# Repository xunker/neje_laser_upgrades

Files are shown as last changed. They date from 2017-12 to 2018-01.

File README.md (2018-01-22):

# neje-laser-upgrades
How-to's and resources for upgrading the NEJE (also sold under the HICTOP brand, and others) desktop USB laser engraver to full GRBL compatibility by replacing
the electronics.

Last updated January, 2018.

## Full grbl upgrade with Arduino CNC Shield

### Videos

I have uploaded a video of the whole upgrade process at [youtu.be/2rbzI-d-bOA](https://youtu.be/2rbzI-d-bOA).

A second video with specific focus on the wiring, and that covers use of a
MOSFET to switch the laser, is also available at [https://youtu.be/MuKYvifYnYs](https://youtu.be/MuKYvifYnYs).

### Links to resources

#### Software-only upgrade

If you are lucky enough to have a machine that can be upgraded without replacing
the board, you can follow [these instructions](http://diyhpl.us/laser_etcher/NEJE_Laser_Etcher/)
to flash a new version of grbl to it.

#### Hardware

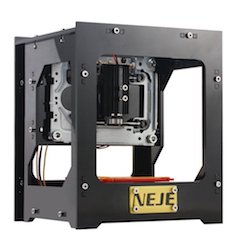
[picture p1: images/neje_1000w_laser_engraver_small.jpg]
NEJE DK-8-KZ Engraver


The engraver pictured above and in the video: [KKmoon NEJE DK-8-KZ 1000mW](https://www.amazon.com/gp/product/B01EACK7UG/ref=oh_aui_detailpage_o05_s02)

The Arduino shield used to control the steppers: [Arduino CNC Shield](http://blog.protoneer.co.nz/arduino-cnc-shield/).
I think I mistakenly referred to this as "grblshield" in the video.

[Arduino Uno](https://www.arduino.cc/en/Main/ArduinoBoardUno), the board that connects to the shield above.

[Laser focus adjustment ring](http://www.thingiverse.com/thing:1939313).

[IRF520 module](https://www.amazon.com/gp/product/B00Z8UF6AQ), the board that
controls power to the 5V laser.

#### Software

[Universal Gcode Sender](https://github.com/winder/Universal-G-Code-Sender) -
Used to send commands to the laser.

[J Tech Photonics Laser Tool](https://jtechphotonics.com/?page_id=2012) -
Used to convert images to laser commands.

#### Wiring diagrams and schematics

##### Connecting PC power supply to Arduino and Shield

The CNC shield can accept any DC voltage from 12V to 36V. Because the stepper
motors used here are very small, the 12V does not need to be high amperage;
500ma or larger will probably be sufficient.

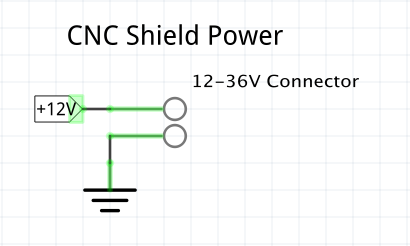
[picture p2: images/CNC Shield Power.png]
CNC Shield Power schematic


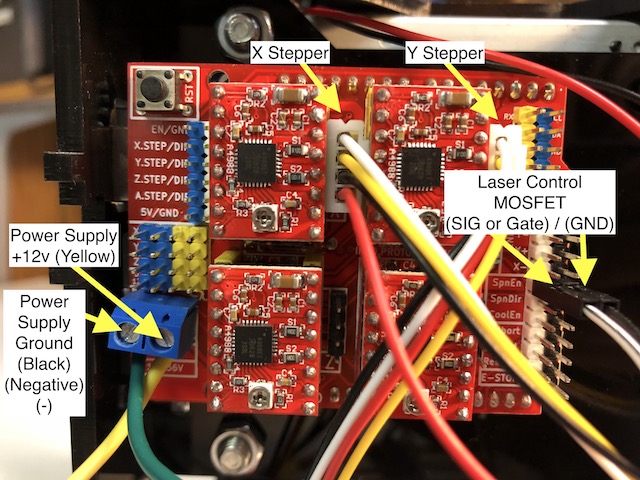
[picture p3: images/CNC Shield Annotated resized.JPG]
CNC Shield Connections annotated


To power the upgrade, I used a power supply designed to run an internal PC
hard drive, although a full-size PC power supply would work.

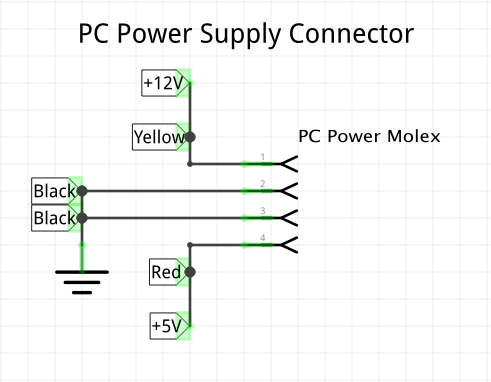
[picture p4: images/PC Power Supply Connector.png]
PC Power Supply Molex schematic


The most important part of the power supply is that is can give 5V at several
amps to power the laser.

The CNC shield electronics can then be powered from 5V as well, but I chose
to power them from the 12V rail of the power supply. If you choose to do that,
you will want to adjust the current-limit on the drivers to avoid damaging the
stepper motors. Details of how to do this are in the video.

##### Connecting stepper motors to the shield

The connector for the stepper motors are between the "drivers" (the red square
  circuit boards [in this image](images/CNC%20Shield%20Annotated%20resized.JPG).

With the white wire facing up, match the 4-pin connector on the cable to the
4-pin connector on the board for both the X- and Y-axis.

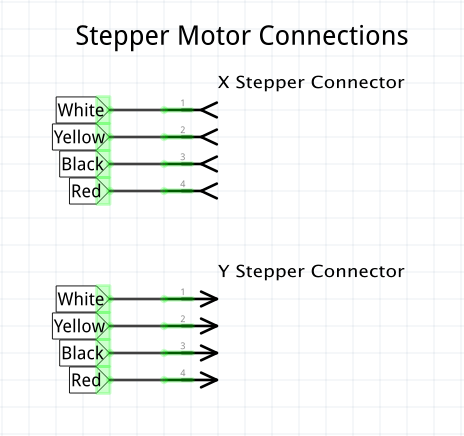
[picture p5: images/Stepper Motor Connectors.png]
Stepper motor connections


##### Connecting laser to power supply and CNC shield

The `SPNEN` (SPiNdle ENable) pin on the shield cannot power the laser itself, so
I use a circuit with a transistor to power the laser from the power supply, but
still allow it to be turned on and off by the CNC shield.

First, you will connect the positive wire of the laser (coloured red on mine) to
the 5V power line from your power supply. It *MUST* be 5V, any more will damage
the laser!

We will switch the laser on and off by connecting or disconnecting the
negative/ground wire. This technique is known as "[low-side switching](https://learn.sparkfun.com/tutorials/transistors/applications-i-switches)".

Here are two ways to do it, though there are probably other ways too. I
recommend using a MOSFET over a TIP120. But if you only have a TIP120 it will
still work though your laser power may suffer.

###### MOSFET circuit

An efficient way to switch the laser on and off is to use an N-Channel Power
MOSFET. Currently I am using an [IRF520 module like this one](https://www.amazon.com/gp/product/B00Z8UF6AQ), but this is not designed for logic-level switching so if you have the option I would
recommend using [a logic-level MOSFET](https://www.mouser.com/ProductDetail/512-FQU13N10LTU) instead.

But, regardless of the voltage, if you want to solder one yourself then the
circuit will look something like this:

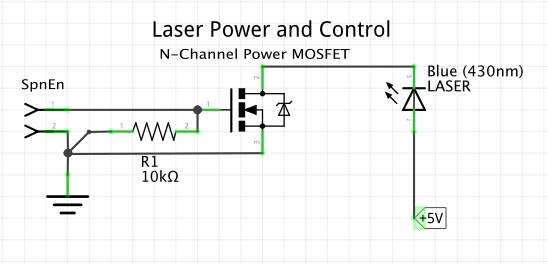
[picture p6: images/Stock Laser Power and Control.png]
MOSFET Laser Trigger schematic


This will switch the laser on and off with a minimum of voltage loss.

If you use the same IRF520 module that I did, here is how the wires are
connected:

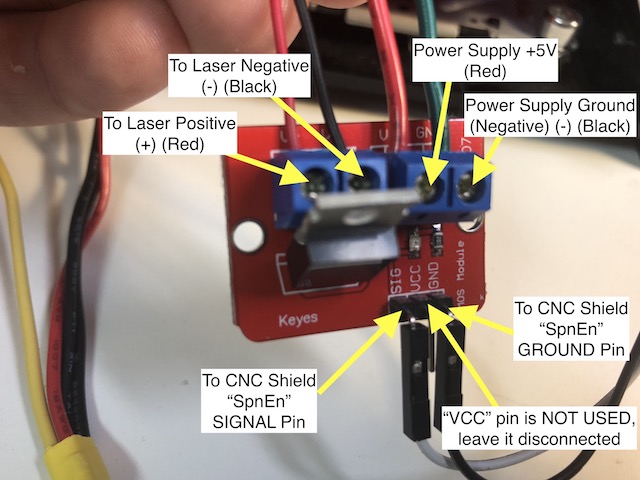
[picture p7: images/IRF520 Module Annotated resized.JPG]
IRF520 module connections


###### TIP120 circuit

Before using the MOSFET, I was using a TIP120 Darlington transistor. This works
but it is a poor choice because the voltage drop on a TIP120 can be as much as
2V in some cases. If we were switching 48V then that wouldn't be a problem but
for a 5V laser, losing even 1V is going to severely impact laser power.

Here is the TIP120 switching circuit I used before:

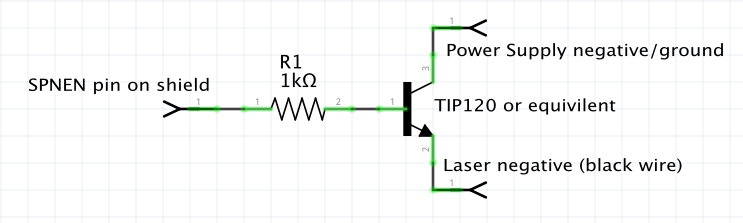
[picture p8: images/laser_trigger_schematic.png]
TIP120 Laser Trigger schematic


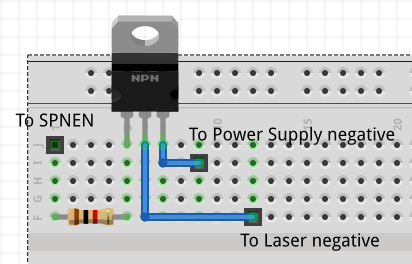
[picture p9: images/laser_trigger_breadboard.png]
TIP120 Laser Trigger breadboard


The transistor I used is a TIP120 "Darlington" transistor. It is a very common
"power transistor" that you can find at any electronics shop (Radio Shack,
Fry's, etc) and everywhere online. You can use any similar NPN-type power
transistor (such as the TIP31, etc) as long as it can handle the current. A
standard 2N3904 transistor can't handle it, and while a 2N2222 *may* be able to
handle it for lower-powered lasers, I would still recommend using a TIP-series transistor because they are still very inexpensive.

**Note**: I should really upgrade the above circuit to use a MOSFET instead
of a power transistor. It shouldn't be that hard adapt it using
[the example from this page](http://www.sensitiveresearch.com/elec/DoNotTIP/index.html). It may also
let us use PWM to control the intensity of the laser.

### Orientation

The origin (X/Y at 0) coordinates should be at the lower-left of the of the
stage. "Lower" here means nearest to front. Make sure moving each axis
negatively will move toward that point, and moving each axis positively will
move away from that point.

### configuring grbl to work in positive space

For J Tech Photonics Laser Tool (in Inkscape), make sure to set the machine
coordinates system to operate in positive space. You will do that by
uncommenting the following line in `config.h` before you upload the grbl
code to the Arduino:

```
#define HOMING_FORCE_SET_ORIGIN
```

### grbl 1.1 settings for Arduino CNC Shield upgrade

```
Grbl 1.1e [‘$’ for help]
$0=10
$1=25
$2=0
$3=0
$4=0
$5=0
$6=0
$10=1
$11=0.010
$12=0.002
$13=0
$20=0
$21=0
$22=0
$23=0
$24=25.000
$25=500.000
$26=250
$27=1.000
$30=1000
$31=0
$32=0
$100=108.000
$101=108.000
$102=250.000
$110=5000.000
$111=5000.000
$112=500.000
$120=500.000
$121=500.000
$122=10.000
$130=27.000
$131=37.000
$132=200.000
```

### Reset default work area

You will probably need to reset the default "work area". Do that with these
two commands:

```
G10 L2 P1 X0 Y0 Z0
G54 X0 Y0 Z0
```

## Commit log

2017-12-01 Added laser trigger pictures, text and fzz, added power supply wiring notes.
    [neje_laser_trigger.fzz]
2017-12-01 Added note about using MOSFET instead of TIP120.
2018-01-22 Added updates for new wiring images and mosfet power circuit.
